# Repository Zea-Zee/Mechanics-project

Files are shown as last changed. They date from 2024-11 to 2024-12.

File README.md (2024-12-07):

# Mechanics project
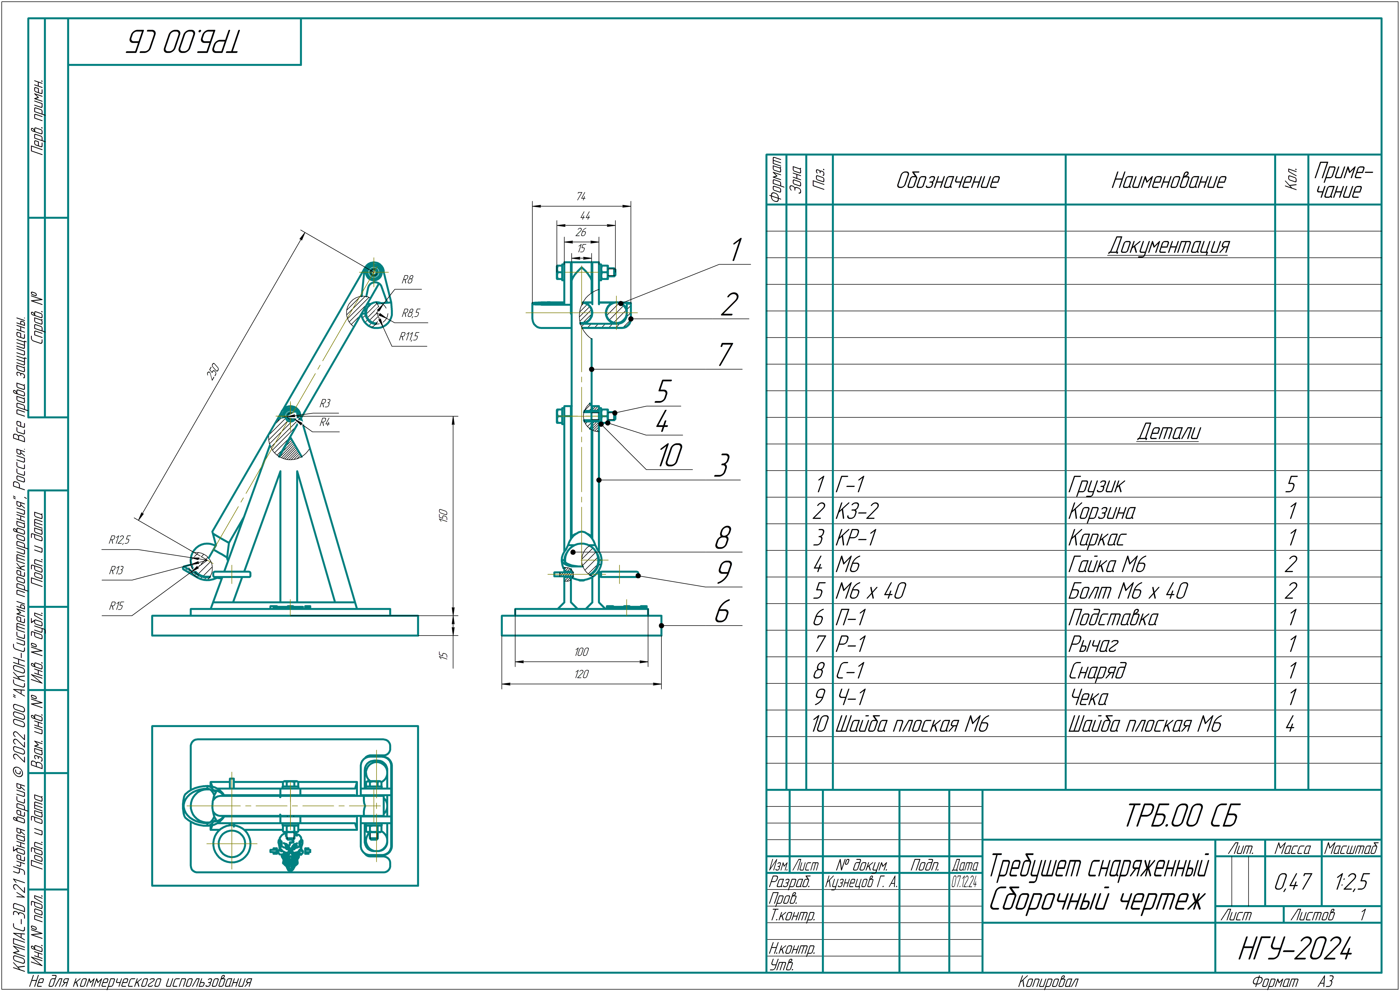
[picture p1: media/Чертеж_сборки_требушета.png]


Дано:

Параметры катапульты:

$$
\alpha_{start}=240^{\circ}\ (начальный\ угол\ снаряда)\\
\alpha_{release}=30^{\circ}\ (угол\ вылета\ снаряда)\\
h_{frame}=0.15м\ (высота\ оси\ вращения\ рычага)\\
l_{arm}=0.25м\ (длина\ всего\ рычага)\\
k_{arm}=0.5\ (соотношение\ плеч\ рычага)\\
m_{arm}=0.018кг\ (масса\ всего\ плеча)
$$

Параметры запуска:

$$
m_{missile}=0.016кг\ (масса\ снаряда)\\
d=0.5м\ (расстояние\ которое\ снаряд\ должен\ пролететь\ от\ станины)\\
R_{missile}=0.008м\ (радиус\ снаряда)
$$

Введем некоторые переменные: (лучше не читать)

$$
\beta_{start\_missile}=\alpha_{start}+90^\circ=240^\circ\ (Угол\ рычага\ снаряда \ в \ начальный\ момент)\\
\beta_{release\_missile}=\alpha_{release}+90^\circ=120^\circ\ (Угол\ рычага\ снаряда \ в \ момент\ вылета )\\
\beta_{start\_weight}=\alpha_{start}+270^\circ=60^\circ\ (Угол\ рычага\ противовеса\ в \ начальный\ момент)\\
\beta_{release\_weight}=\alpha_{release}+270^\circ=300^\circ\ (Угол\ рычага\ противовеса\ в \ момент\ вылета)\\

l_{missile\_arm}=l_{missile}*(1-k_{arm})=0.125м\ (длина\ плеча\ снаряда)\\
l_{weight\_arm}=l_{missile}*k_{arm}=0.125м\ (длина\ плеча\ противовеса)\\
$$

Теперь рассчитаем положения снаряда и противовеса: (лучше не читать)

$$
x_{start\_missile}=\cos(\beta_{start\_missile})*l_{missile\_arm\_length}\\
y_{start\_missile}=\sin(\beta_{start\_missile})*l_{missile\_arm\_length}+h_{frame}\\

x_{start\_weight}=\cos(\beta_{start\_weight})*l_{_weight\_arm\_length}\\
y_{start\_weight}=\sin(\beta_{start\_weight})*l_{_weight\_arm\_length}+h_{frame}\\

x_{release\_missile}=\cos(\beta_{release\_missile})*l_{missile\_arm\_length}\\
y_{release\_missile}=\sin(\beta_{release\_missile})*l_{missile\_arm\_length}+h_{frame}\\

x_{release\_weight}=\cos(\beta_{release\_weight})*l_{_weight\_arm\_length}\\
y_{release\_weight}=\sin(\beta_{release\_weight})*l_{_weight\_arm\_length}+h_{frame}
$$

Рассчитаем начальную скорость v0 под углом вылета:

$$
x=x_{start\_missile}+v_0\cos(\alpha_{release})t\\

y=y_{start\_missile}+v_0\sin(\alpha_{release})t-\frac{gt^2}{2}\\
\\

Выразим\ t\ через\ x\\
t=\frac{x-x_{start\_missile}}{v_0\cos(\alpha_{release})}\\

Подставим\ в\ y\\
y=y_{start\_missile}+v_0\sin(\alpha_{release})(\frac{x-x_{start\_missile}}{v_0\cos(\alpha_{release})})-\frac{g(\frac{x-x_{start\_missile}}{v_0\cos(\alpha_{release})})^2}{2}\\

Упростим\\
y=y_{start\_missile}+(x-x_{start\_missile})\tan(\alpha_{release})-\frac{g(x-x_{start\_missile})^2}{2v_0\cos(\alpha_{release})}\\
\\

Выразим\ v_0\\
v_0=\frac{g(x-x_{start\_missile})^2}{2\cos^2(\alpha_{release})[(x-x_{start\_missile})\tan(\alpha_{release})-(y-y_{start\_missile})]}\\

Посчитаем\ v_0\\
v_0=\frac{9.81м/с^2 * (0.5м-(-0.0625м))^2}{2*0.75*[(0.5м-(-0.0625м))*0,578-(0м-0.258м)]}=1.90м/с
$$

Теперь выведем время полета, и закон движения:

$$
v_x=v_0\cos(\alpha_{release})=1.64м/с\ (скорость\ снаряда\ по\ x)\\
v_y=v_0\sin(\alpha_{release})=0.95м/с\ (скорость\ снаряда\ по\ y)\\

t_{path1}=\frac{v_y}{g}=0.0967с\ (время\ полета\ до\ наивысшей\ точки)\\
y_{max}=y_{release\_missile}+v_yt_{path1}-\frac{gt_{path1}^2}{2}=0.304м\ (наивысшая \ точка\ полета)\\
Из\ закона\ движения\ y\ выразим\ \\
t_{path2}=\frac{\sqrt{2y_{max}}}{g}=0.249с\\
t_{tot}=t_{path1}+t_{path2}=0.3456с
$$

Missile start point: (-0.06250000000000006; 0.041746824526945184)
Weight start point: (0.06250000000000006; 0.2582531754730548)
Missile release point: (-0.06249999999999997; 0.2582531754730548)
Weight release point: (0.06249999999999997; 0.041746824526945156)
239.99999999999997 119.99999999999999
0.21650635094610965
Launching missile with angle: 30.00 degrees and v0: 1.88 m/s
Weight mass: 0.03438221420742506
Vx: 1.6312813025047181, Vy: 0.9418206991251022
first_path_time 0.09603898366160742
max_y 0.3034789268407745
second_path_time 0.24878198568090912
total_time 0.34482096934251655
Flight time: 0.34482096934251655 s, x_move: 0.5624999999999999 m, y_move: -0.25825317547305493 m
Landed in: (0.4999999999999999; -1.1102230246251565e-16)

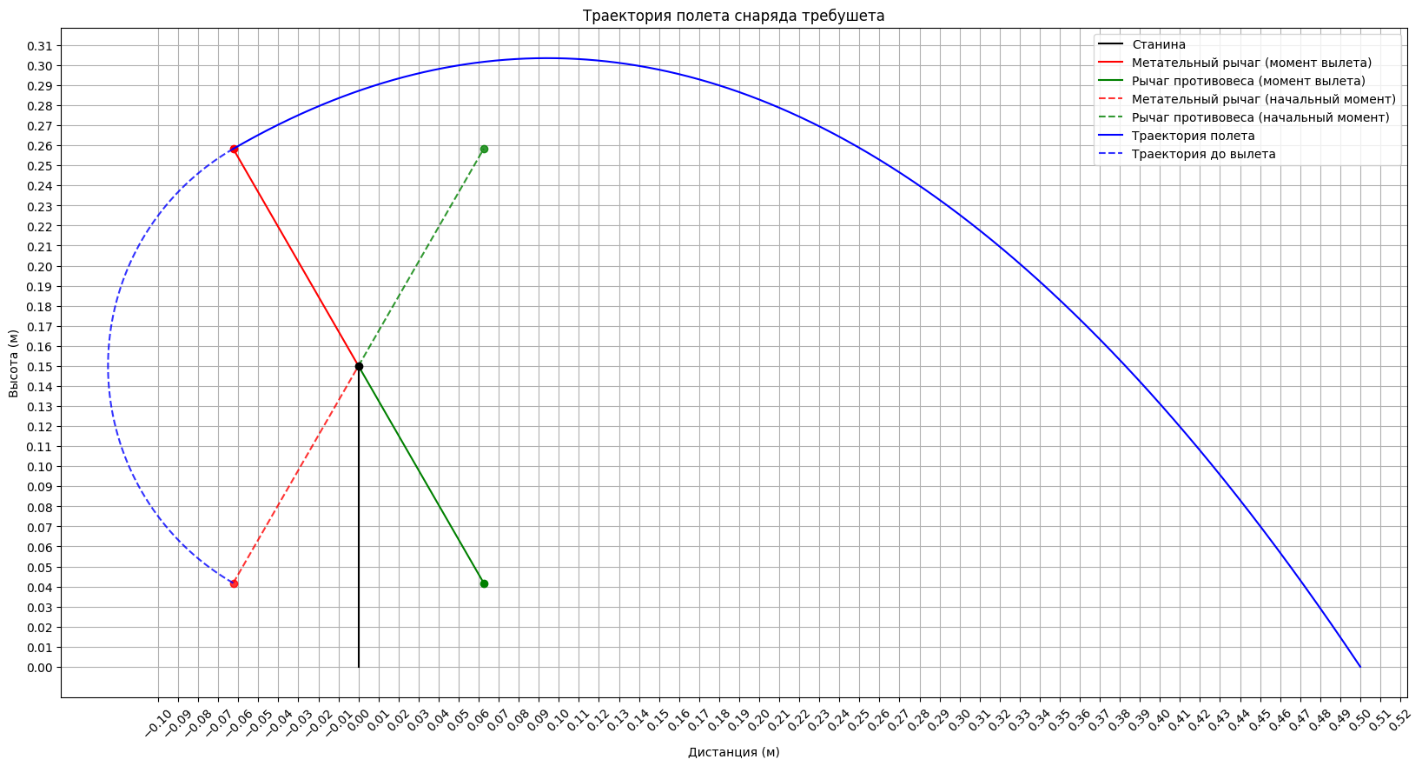
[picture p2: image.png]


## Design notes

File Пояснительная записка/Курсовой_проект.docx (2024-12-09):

МИНИСТЕРСТВО НАУКИ И ВЫСШЕГО ОБРАЗОВАНИЯ
РОССИЙСКОЙ ФЕДЕРАЦИИ

НОВОСИБИРСКИЙ ГОСУДАРСТВЕННЫЙ УНИВЕРСИТЕТ

Курсовая проект по дисциплине:

«МЕХАНИКА»

Проектирование механической модели требушета

Факультет: Институт Интеллектуальной Робототехники

Группа: 22932

Студенты: | Оценка
Кадиленко Иван
Кузнецов Глеб

Преподаватель: Сахнов А.Ю.

НОВОСИБИРСК

2024

1. Задание на курсовую работу.

1. Метание деформируемого снаряда любой выбранной массы и формы на расстояние от 30 см до 60 см и отклонением от центральной оси не более 30°.

2. Нахождение модели во взведённом состоянии без приложения посторонних сил (без помощи человека).

3. Механический спуск.

4. Целостность и устойчивость конструкции в течение 3-х попыток метания.

2. Эскиз модели.

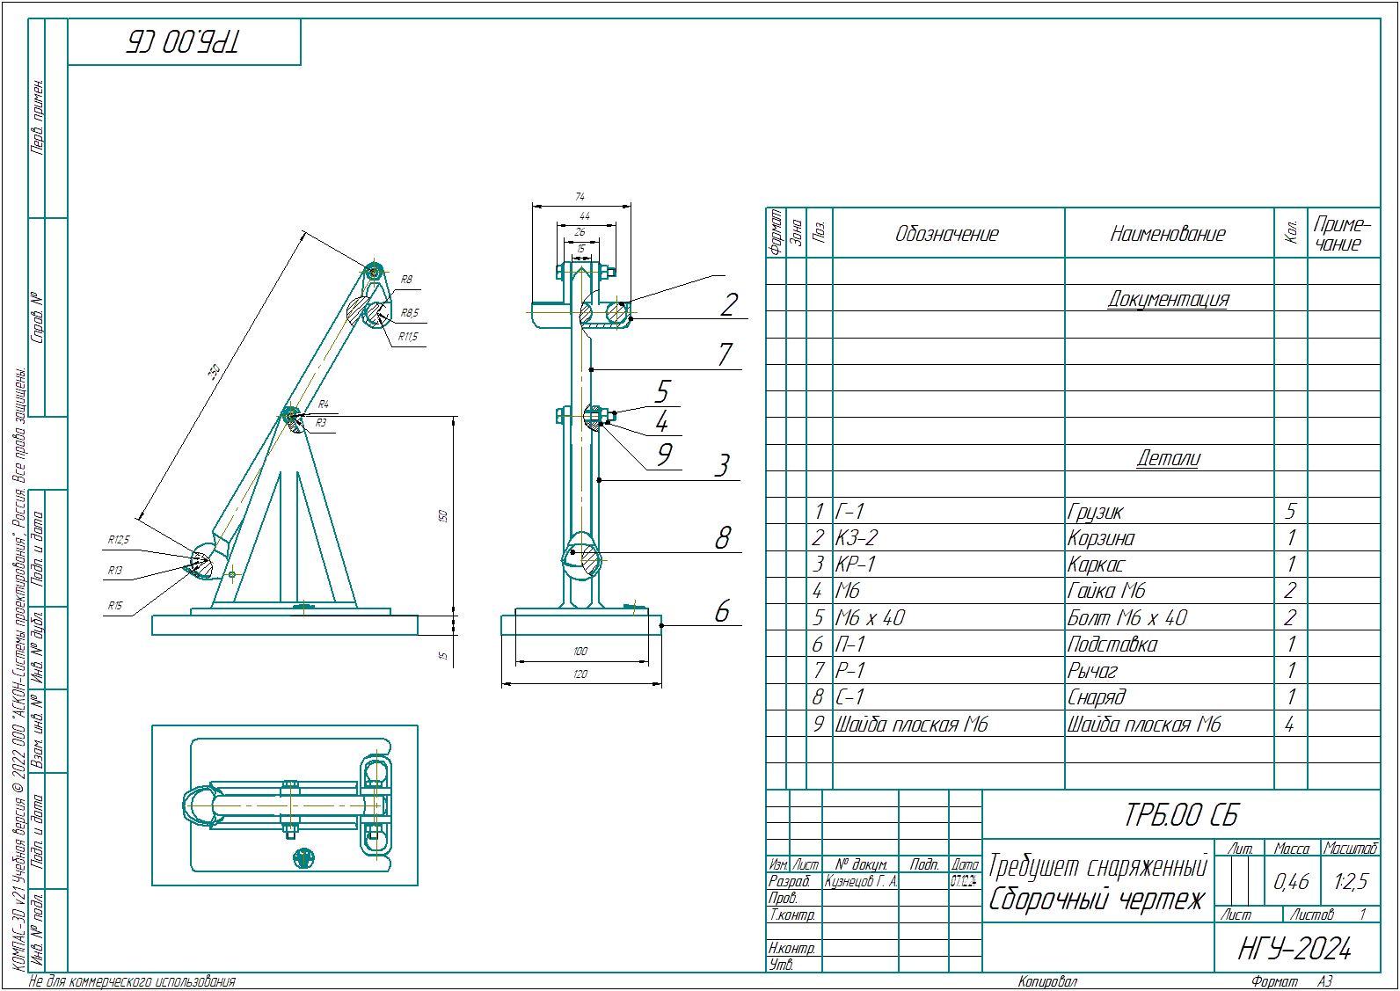
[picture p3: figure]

Рисунок 1. Чертёж модели. Размеры в мм

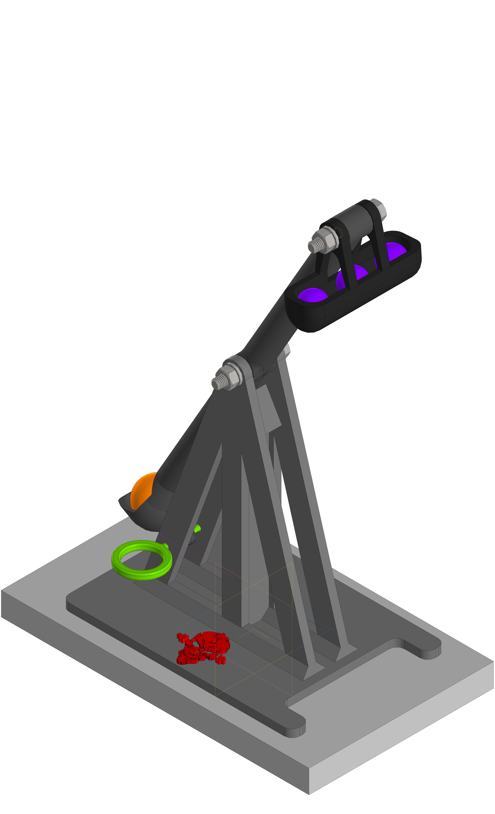
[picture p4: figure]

Рисунок 2. Модель требушета в изометрии.

3. Динамический анализ механической модели (Расчёт разгона снаряда)

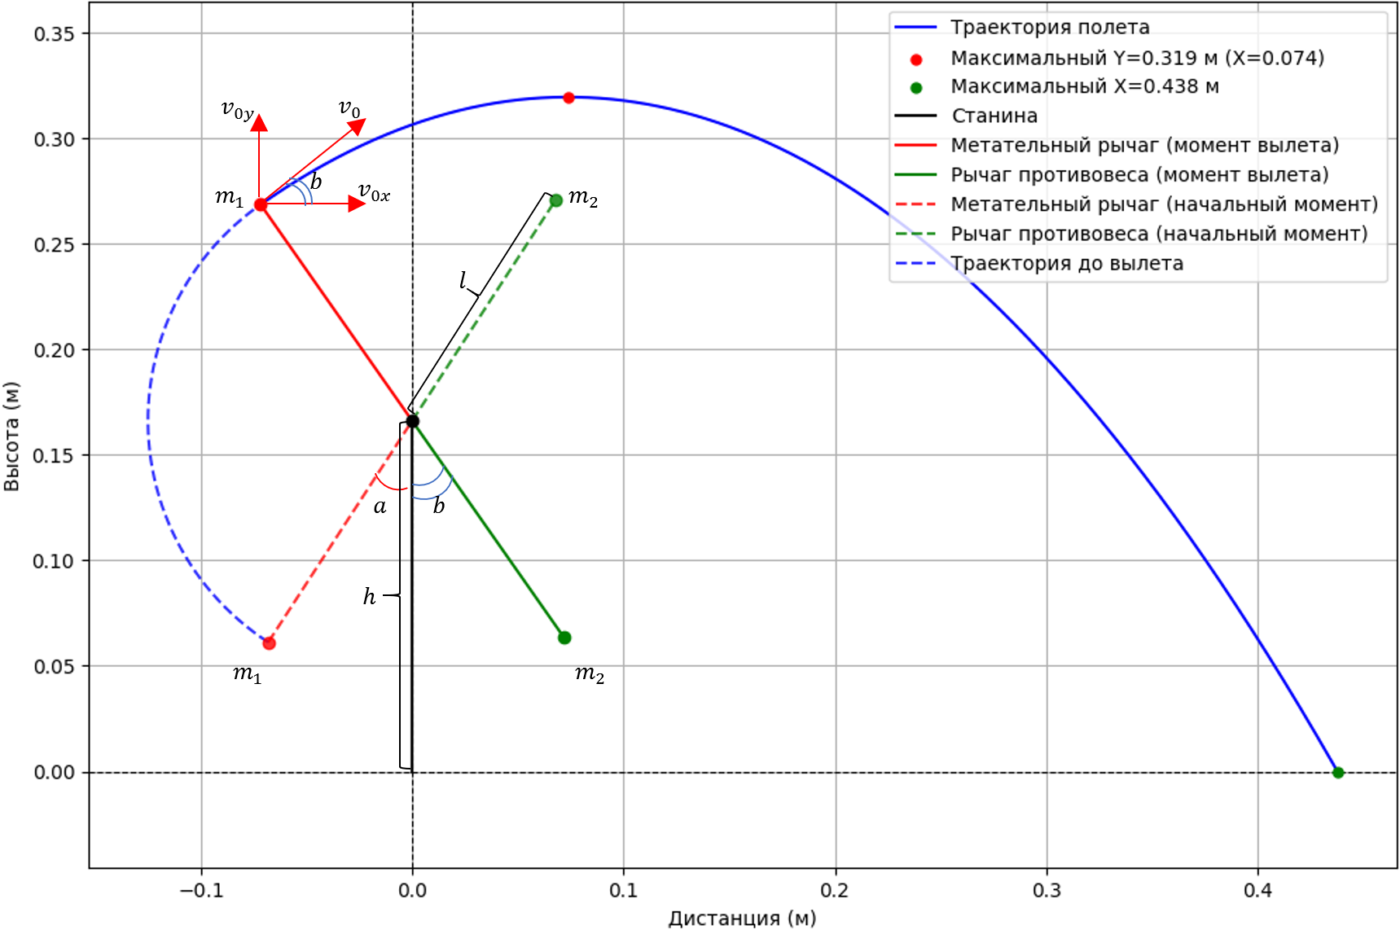
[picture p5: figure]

Рисунок 3. Схема работы требушета с параметрами.

Введём переменные, которые потребуются для расчётов, в скобках указаны значения нашего требушета:

m_1 – Масса снаряда (0.0111 кг)

m_2 – Масса противовеса (0.0765 кг)

m_r – Масса рычага (0.019 кг)

l – Расстояние от конца рычага до оси вращения (0.125 м)

g – Ускорение свободного падения (9.81 м/c^2 )

a – Стартовый угол (33°)

b – Угол вылета (35°)

b' - Угол вылета, измеренный в ту же сторону что и стартовый угол (145°)

Для нахождения скорости вылета снаряда, запишем уравнение баланса энергий для начального момента и момента вылета

E_(Im_2)^п =E_(IIm_1)^п +E_(IIm_1)^к +E_(IIm_2)^к

h^(') =l*(cos(a)+cos(b)) – Разница высоты между начальным моментом и моментом вылета

E_(Im_2)^п =m_2 *g*h' - Потенциальная энергия снаряда в начальный момент

E_(IIm_1)^п =m_1 *g*h' - Потенциальная энергия снаряда в момент вылета

E_(IIm_1)^к =(m_1 *v^2)/2 – Кинетическая энергия снаряда в момент вылета

E_(IIm_2)^к =(m_2 *v^2)/2 – Кинетическая энергия противовеса в момент вылета. Учитываем мы её т.к. в момент вылета противовес бьётся об ограничитель. Согласно теореме Карно, эта энергия равна кинетической энергии противовеса в момент удара об ограничитель.

Получаем следующее выражение

m_2 *g*h^(') =m_1 *g*h^(') +(m_1 *v^2)/2+(m_2 *v^2)/2

Выразим скорость

v^2 =(2*g*l*h^(') *(m_2 -m_1 ))/(m_2 +m_1)

Подставим h' и получим итоговое уравнение скорости вылета снаряда

v_0 =√((2*g*l*(cos(a)+cos⁡(b))*(m_2 -m_1 ))/(m_2 +m_1))

Подставим наши значения и получим скорость вылета снаряда

v_0 =1.742 м/c

4. Кинематический анализ механической модели (Расчёт траектории полёта снаряда)

Введём переменные, которые потребуются для расчётов, в скобках указаны значения нашего требушета:

v_0 - Скорость снаряда в момент вылета (1.742 м/с)

h - Высота оси вращения (0.15 м)

shift – Смещение от точки пуска по оси Х до оси вращения (0.07 м)

Рассчитаем высоту запуска

h_l =h+l*cos⁡(b)

Рассчитаем время полета снаряда до момента пересечения высоты запуска по оси Y

v_y → -v_y

t_1 =(v_y -(-v_y ))/g=(2v_y)/g=2v_y *(sin(b))/g

Найдём оставшееся время полёта снаряда

h_l =v_y *t+(gt^2)/2

gt^2 +2v*sin(b)-2h_l =0

D=(2*v*sin(b))^2 +8*g*h_l

t_2 =(-2*v*sin(b)+√D)/(2g)

Общее время полёта

t=t_1 +t_2

По X нет ускорения, составим уравнение

x=v_0 *cos(b)*t-shift

Уравнение по Y

y=v_0 *sin(b)*t-1/2*gt^2 +h_l

Подставим скорость вылета снаряда и получим дальность

x=0.438 м

5. Обоснование устойчивости механической модели (Определение центра тяжести)

Проведём теоретический расчёт центра масс требушета. Учитывая симметрию требушета относительно вертикальной плоскости, достаточной найти координаты центра тяжести в проекции на данную плоскость. Формула для нахождения центра масс в общем виде для k элементов:

X=(∑_(i=1)^k X_i *m_i)/(∑_(i=1)^k m_i)

Подставим наши значения (второе слагаем умножено на 3, т.к. мы используем 3 противовеса)

X=(0.168*0.01+0.168*(0.0168*3)+0.104*0.019+0.041*0.0111+0.102*0.066+0.104*0.2755)/(0.01+(0.0168*3)+0.019+0.0111+0.066+0.2755)

Y=(0.253*0.01+0.242*(0.0168*3)+0.165*0.019+0.057*0.0111+0.07*0.066+0.0075*0.2755)/(0.01+(0.0168*3)+0.019+0.0111+0.066+0.2755)

Вычислим значения центра масс

X≈0.111 м

Y≈0.06 м

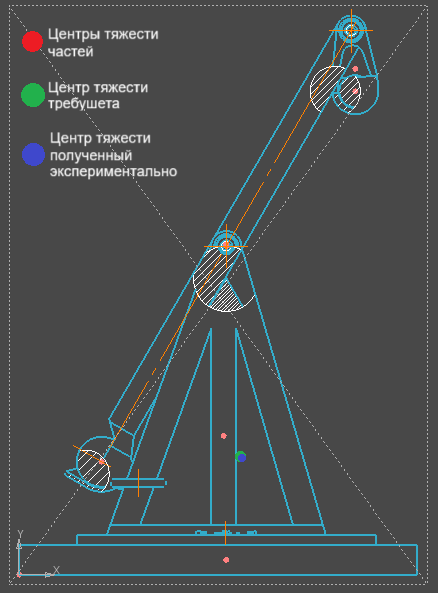
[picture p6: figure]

Рисунок 4. Теоретически рассчитанный центр масс требушета

Рассчитаем центр масс экспериментально методом подвешивания.

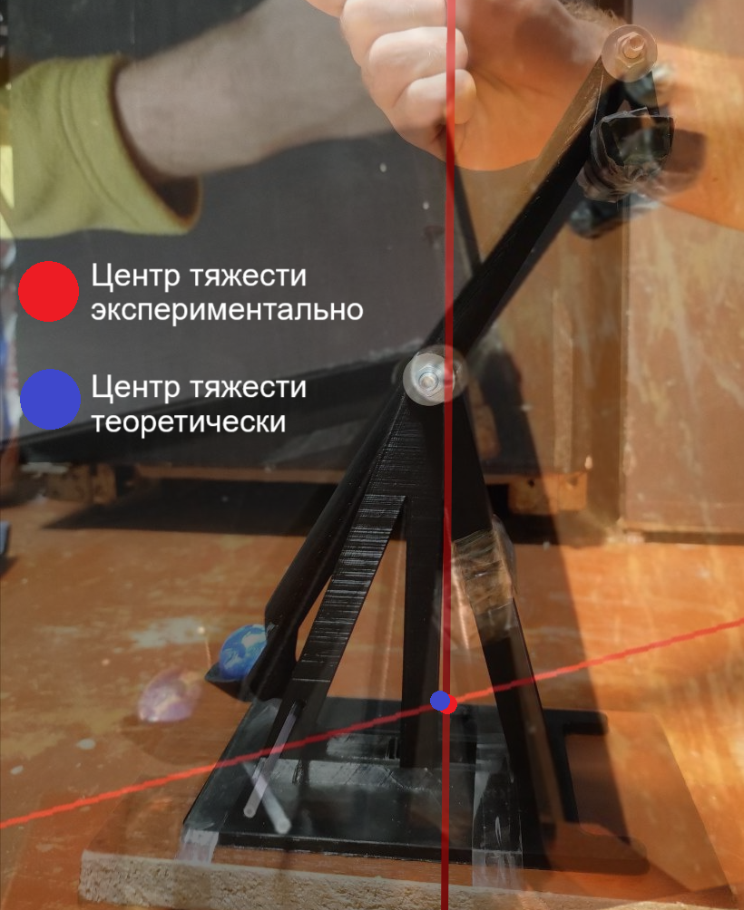
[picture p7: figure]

Рисунок 5. Экспериментально рассчитанный центр тяжести требушета.

Как можно увидеть мы получили достаточно точное совпадение центров тяжести.

6. Сравнение фактических параметров механической модели с расчётными параметрами.

Проведя 3 пуска, были получены следующие результаты: 0.475 м, 0.45 м, 0.48 м.

X_(факт) =(0.475+0.45+0.48)/3=0.468 м

Рассчитаем абсолютную и относительную погрешности

ΔX_(абс) =0.468-0.438=0.03 м

δ=(0.468-0.438)/0.468*100%=6.48%

Такая разница в фактические и расчётные значения может быть вызвана тем, что мы учитываем удар плеча об ограничитель как абсолютно неупругий удар, что может быть не совсем верно.

7. Описание электронной модели механической системы

Программа запускается при помощи python, на вход её подаются все значения, нужные для расчёта. Если никакие значения не будут переданы, будут взяты значения нашего требушета.

Запуск: py calculation.py

Передаваемые параметры:

--m1 - Масса снаряда.

--m2 – Масса противовеса

--h – Высота оси вращения

--l – Длина плеча (от оси до края рычага).

--alpha – Начальный угол

--beta – Угол вылета

--is_shift - Учитывать ли смещение точки вылета по X относительно оси вращения.

--visualize - Выводить ли визуализацию.

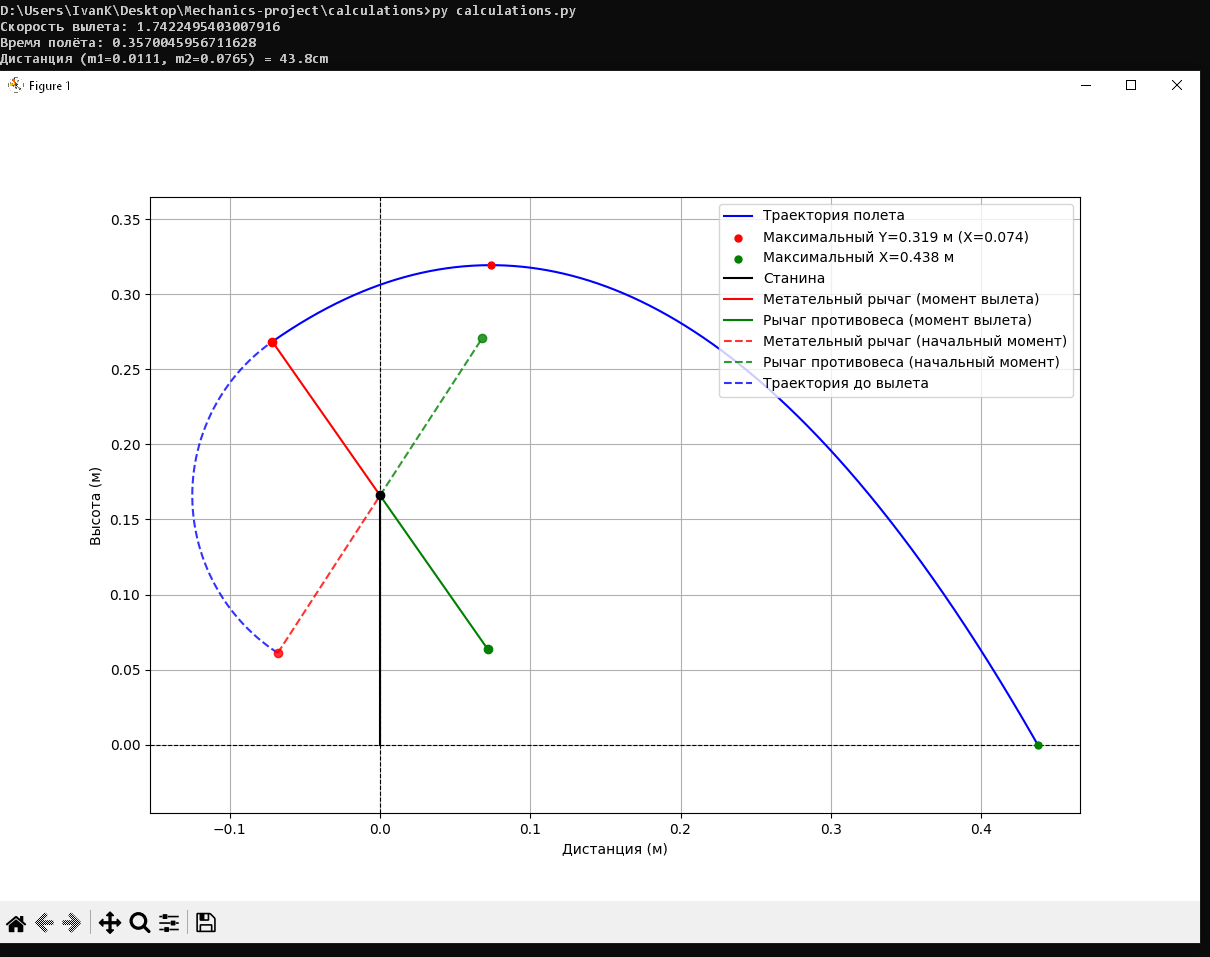
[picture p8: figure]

Рисунок 6. Пример работы программы.

Листинг кода:

import math

import numpy as np

import matplotlib.pyplot as plt

import argparse

G = 9.81

def calculate_r(m1, m2, ma, h, l, a1, a2, is_shift=False, visualize=False):

'''

m1 - mass of projectile \n

m2 - mass of counterweight \n

ma - mass of lever \n

h - height of mount \n

l - length of lever \n

a1 - start angle \n

a2 - finish angle (Measured in the opposite direction from the starting point) \n

shift - difference between middle of trebushet and position of throw \n

visualise - visualise trajectory \n

'''

a1r = np.radians(a1)

a2r = np.radians(a2)

speed = np.sqrt((2*G*l*(np.cos(a1r) + np.cos(a2r))*(m2-m1))/(m1+m2))

print('Скорость вылета:', speed)

t1 = (2*speed*np.sin(a2r))/G

x1 = t1*speed*np.cos(a2r)

heigth_of_launch = h + l*np.cos(a2r)

D = (2*speed*np.sin(a2r))**2 + 8*G*(heigth_of_launch)

t2 = (-2*speed*np.sin(a2r) + np.sqrt(D))/(2*G)

x2 = speed*np.cos(a2r)*t2

print('Время полёта:', t1+t2)

length = x1+x2

if is_shift:

shift = l * np.sin(a2r)

length -= shift

else:

shift = 0

print(f'Дистанция (m1={m1}, m2={m2}) = {length*100:.1f}cm')

if visualize:

t1_arr = np.linspace(0, t1+t2, num=10000, endpoint=False)

x1_arr = speed*np.cos(a2r)*t1_arr - shift

y1_arr = speed*np.sin(a2r)*t1_arr - 1/2*G*(t1_arr**2) + heigth_of_launch

plt.figure(figsize=(12,8))

plt.plot(x1_arr, y1_arr, color='blue', label='Траектория полета')

plt.scatter(x1_arr[np.where(y1_arr == np.max(y1_arr))][0], np.max(y1_arr), color='red', s=25, zorder=10, label=f'Максимальный Y={np.max(y1_arr):.3f} м (X={x1_arr[np.where(y1_arr == np.max(y1_arr))][0]:.3f})')

plt.scatter(x1_arr[-1], 0, color='green', s=25, zorder=10, label=f'Максимальный X={x1_arr[-1]:.3f} м')

plt.plot([0, 0], [0, h], label='Станина', color="black")

plt.plot([-l*np.sin(a2r), 0], [h+l*np.cos(a2r), h], label='Метательный рычаг (момент вылета)', color='red')

plt.plot([0, l*np.sin(a2r)], [h, h-l*np.cos(a2r)], label='Рычаг противовеса (момент вылета)', color='green')

plt.plot([-l*np.sin(a1r), 0], [h-l*np.cos(a1r), h], label='Метательный рычаг (начальный момент)', color='red', linestyle='--', alpha=0.8)

plt.plot([0, l*np.sin(a1r)], [h, h+l*np.cos(a1r)], label='Рычаг противовеса (начальный момент)', color='green', linestyle='--', alpha=0.8)

plt.plot(0, h, marker='o', color='black')

plt.plot(-l*np.sin(a2r), h+l*np.cos(a2r), marker='o', zorder=10, color='red')

plt.plot(l*np.sin(a2r), h-l*np.cos(a2r), marker='o', zorder=10, color='green')

plt.plot(-l*np.sin(a1r), h-l*np.cos(a1r), marker='o', zorder=10, color='red', alpha=0.8)

plt.plot(l*np.sin(a1r), h+l*np.cos(a1r), marker='o', zorder=10, color='green', alpha=0.8)

pre_release_t = np.linspace(np.radians(270-a1), np.radians(90+a2), num=1000)

pre_release_x = np.cos(pre_release_t) * l

pre_release_y = h + np.sin(pre_release_t) * l

plt.plot(pre_release_x, pre_release_y, label='Траектория до вылета', color='blue', linestyle='--', alpha=0.8)

plt.axhline(0, color='black', linestyle='--', linewidth=0.8)

plt.axvline(0, color='black', linestyle='--', linewidth=0.8)

plt.xlabel('Дистанция (м)')

plt.ylabel('Высота (м)')

plt.legend(loc='upper right')

plt.grid()

plt.axis('equal')

plt.show()

return length

def main():

ball = 0.0168

jump_ball = 0.0111

fixing = 0.009 + 0.0025 + 0.0025 * 2 #= 0.0165

backet = [0.010, 0.027, 0.043, 0.060, 0.077]

lever_mass = 0.019

frame_mass = 0.066

# Длины в метрах

lever_length = 0.125

frame_heigth = 0.151

bruss_heigth = 0.015

# Углы в градусах

alpha = 33

beta = 35

parser = argparse.ArgumentParser()

parser.add_argument("--m1", default=jump_ball,

help="Масса снаряда.", type=float)

parser.add_argument("--m2", default=backet[3]+fixing,

help="Масса противовеса.", type=float)

parser.add_argument("--ma", default=lever_mass,

help="Масса рычага.", type=float)

parser.add_argument("--h", default=frame_heigth + bruss_heigth,

help="Высота оси вращения.", type=float)

parser.add_argument("--l", default=lever_length,

help="Длина плеча (от оси до края рычага).", type=float)

parser.add_argument("--alpha", default=alpha,

help="Начальный угол.", type=float)

parser.add_argument("--beta", default=beta,

help="Угол вылета.", type=float)

parser.add_argument("--is_shift", default=True,

help="Учитывать ли смещение точки вылета по X относительно оси вращения.", type=bool)

parser.add_argument("--visualize", default=True,

help="Выводить ли визуализацию.", type=bool)

m1 = parser.parse_args().m1

m2 = parser.parse_args().m2

ma = parser.parse_args().ma

h = parser.parse_args().h

l = parser.parse_args().l

a1 = parser.parse_args().alpha

a2 = parser.parse_args().beta

is_shift = parser.parse_args().is_shift

visualize = parser.parse_args().visualize

calculate_r(m1, m2, ma, h, l, a1, a2, is_shift, visualize)

if __name__ == "__main__":

main()

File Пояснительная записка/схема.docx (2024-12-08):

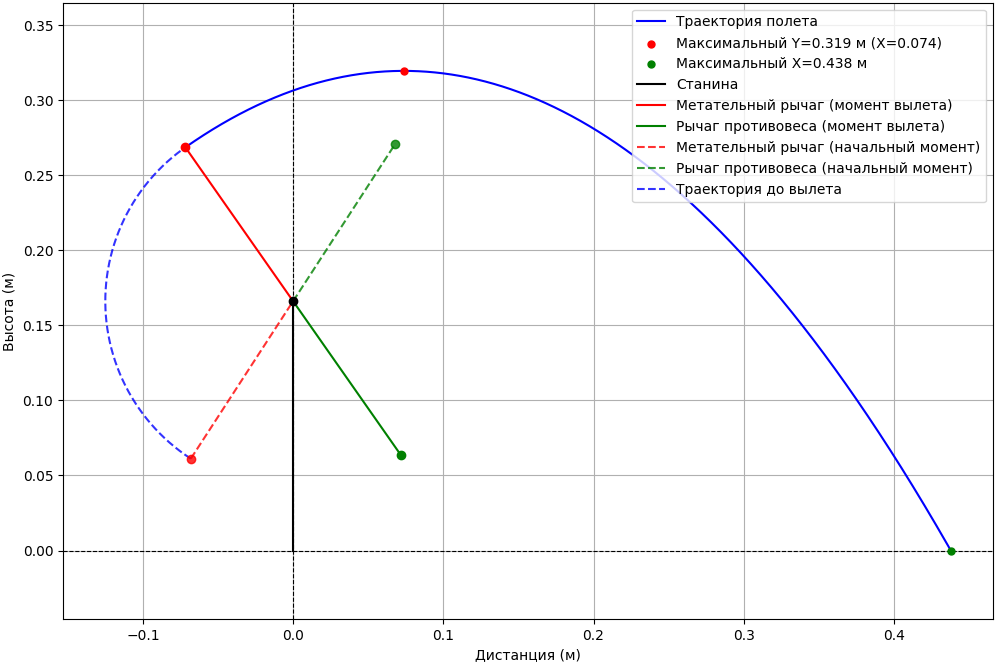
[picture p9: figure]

b

v_(0x)

v_0

v_(0y)

h

l

m_1 m_2

m_1 m_2

a b

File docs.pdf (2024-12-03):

Mechanics project | 1

# Mechanics project

## Дано:

## Параметры катапульты:

## Параметры запуска:

## Введем некоторые переменные: (лучше не читать)

## Теперь рассчитаем положения снаряда и противовеса: (лучше не читать)

## Рассчитаем начальную скорость v0 под углом вылета:

# αstart = 240 (начальный угол снаряда)

∘

# αrelease = 30 (угол вылета снаряда)

∘

# hf rame = 0.15м (высота оси вращения рычага) larm = 0.25м (длина всего рычага) karm = 0.5 (соотношение плеч рычага) marm = 0.018кг (масса всего плеча)

# mmissile = 0.016кг (масса снаряда) d = 0.5м (расстояние которое снаряд должен пролететь от станины) Rmissile = 0.008м (радиус снаряда)

βstart_missile = αstart + 90 =

# ∘ 240 (Угол рычага снаряда в начальный момент)

∘

βrelease_missile = αrelease + 90 =

# ∘ 120 (Угол рычага снаряда в момент вылета)

∘

βstart_weight = αstart + 270 =

# ∘ 60 (Угол рычага противовеса в начальный момент)

∘

βrelease_weight = αrelease + 270 =

# ∘ 300 (Угол рычага противовеса в момент вылета)

∘

lmissile_arm = lmissile ∗ (1 − karm) = 0.125м (длина плеча снаряда)

# lweight_arm = lmissile ∗ karm = 0.125м (длина плеча противовеса)

xstart_missile = cos(βstart_missile ) ∗ lmissile_arm_length

ystart_missile = sin(βstart_missile ) ∗ lmissile_arm_length + hf rame

xstart_weight = cos(βstart_weight) ∗ lweight_arm_length

ystart_weight = sin(βstart_weight) ∗ lweight_arm_length + hf rame

xrelease_missile = cos(βrelease_missile ) ∗ lmissile_arm_length

yrelease_missile = sin(βrelease_missile ) ∗ lmissile_arm_length + hf rame

xrelease_weight = cos(βrelease_weight) ∗ lweight_arm_length

yrelease_weight = sin(βrelease_weight) ∗ lweight_arm_length + hf rame

## Теперь выведем время полета, и закон движения:

## Missile start point: (-0.06250000000000006; 0.041746824526945184) Weight start point: (0.06250000000000006; 0.2582531754730548) Missile release point: (-0.06249999999999997; 0.2582531754730548) Weight release point: (0.06249999999999997; 0.041746824526945156)

239.99999999999997 119.99999999999999
0.21650635094610965

## Launching missile with angle: 30.00 degrees and v0: 1.88 m/s Weight mass: 0.03438221420742506

x = xstart_missile + v0 cos(αrelease )t

y = ystart_missile + v0 sin(αrelease )t −
2

gt

2

# Выразим t через x

t =
v0 cos(αrelease )

x − xstart_missile

# Подставим в y

y = ystart_missile + v0 sin(αrelease )( | ) −
v0 cos(αrelease )

x − xstart_missile
2
g( | )
v0 cos(αrelease )

x−xstart_missile 2

# Упростим

y = ystart_missile + (x − xstart_missile )tan(αrelease ) − 2v0 cos(αrelease )

g(x − xstart_missile )

2

# Выразим v0

v0 =
2 cos (α | )[(x − x | )tan(α | ) − (y − y | )]
2
release | start_missile | release | start_missile
| | g(x − xstart_missile )

2

| | Посчитаем v0
v0 = | =

# 2 ∗ 0.75 ∗ [(0.5м − (−0.0625м)) ∗ 0, 578 − (0м − 0.258м)]

# 9.81м/с ∗ (0.5м − (−0.0625м))

2 2
| | | | 1.90м/с

# vx = v0 cos(αrelease ) = 1.64м/с (скорость снаряда по x) vy = v0 sin(αrelease ) = 0.95м/с (скорость снаряда по y)

tpath1 = =
g
vy | 0.0967с (время полета до наивысшей точки)
ymax = yrelease_missile + vy tpath1 − | =
2

gt
path1

2

# 0.304м (наивысшая точка полета) Из закона движения y выразим

tpath2 = | =
g

# 2ymax 0.249с

ttot = tpath1 + tpath2 = 0.3456с

## Vx: 1.6312813025047181, Vy: 0.9418206991251022 first_path_time 0.09603898366160742 max_y 0.3034789268407745 second_path_time 0.24878198568090912 total_time 0.34482096934251655 Flight time: 0.34482096934251655 s, x_move: 0.5624999999999999 m, y_move:

-0.25825317547305493 m

## Landed in: (0.4999999999999999; -1.1102230246251565e-16)


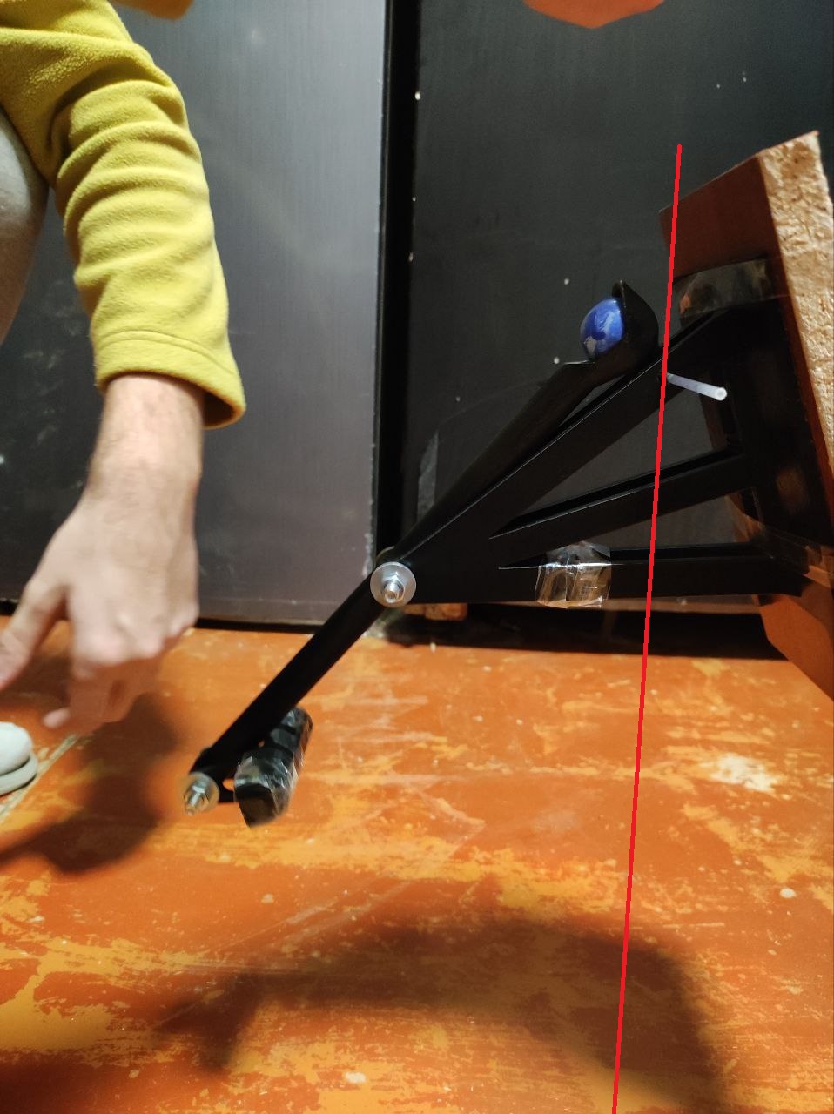
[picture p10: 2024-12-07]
media/Подвес_1.jpg

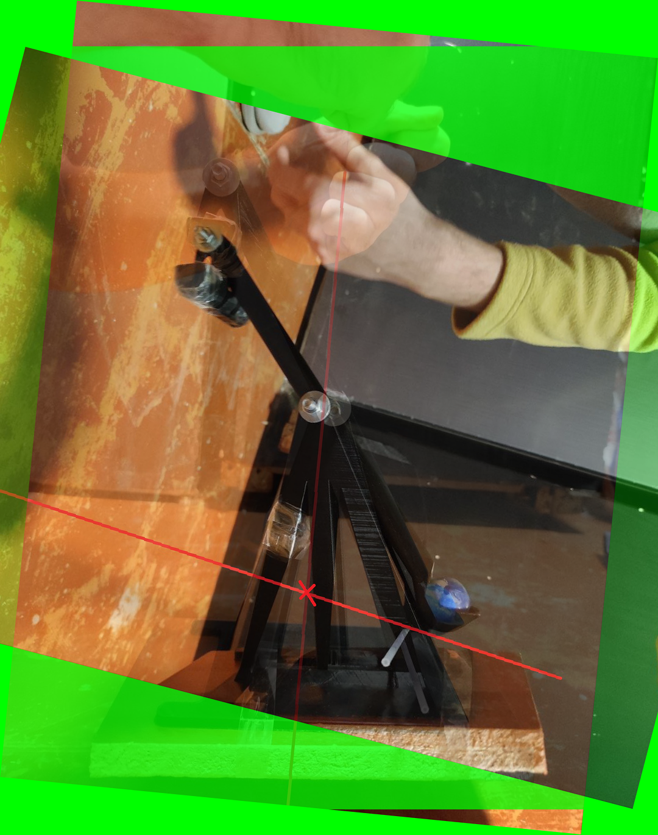
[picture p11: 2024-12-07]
media/Пересечение.png

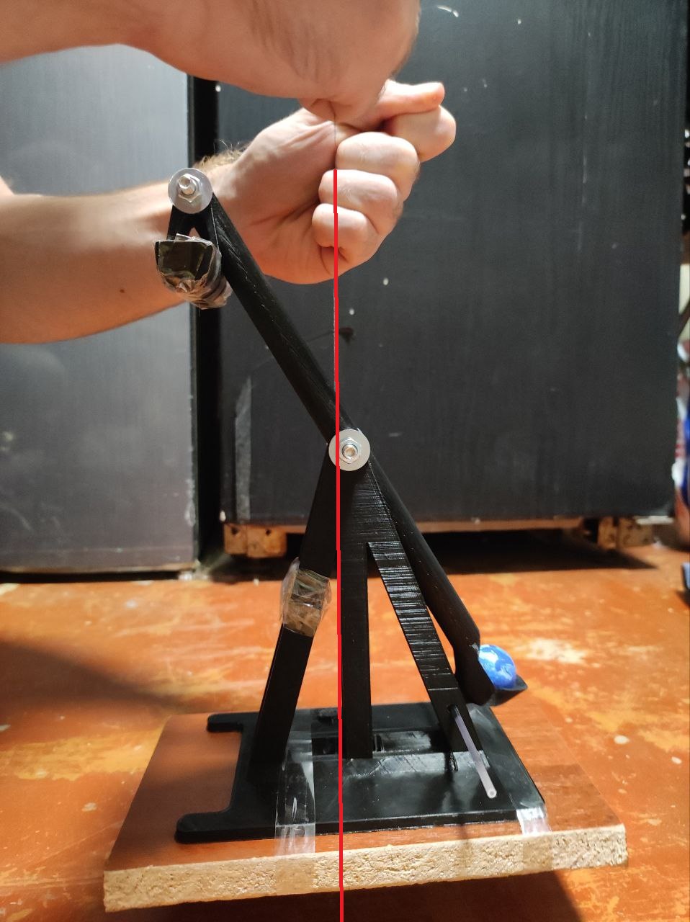
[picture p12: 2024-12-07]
media/Подвес_2.jpg

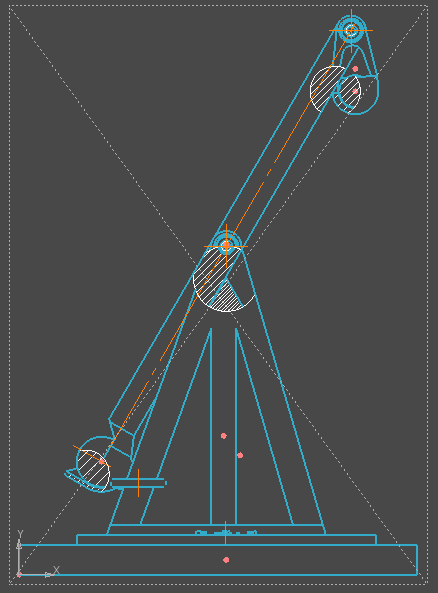
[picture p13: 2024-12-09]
Пояснительная записка/цунтр масс теория + деталей.png

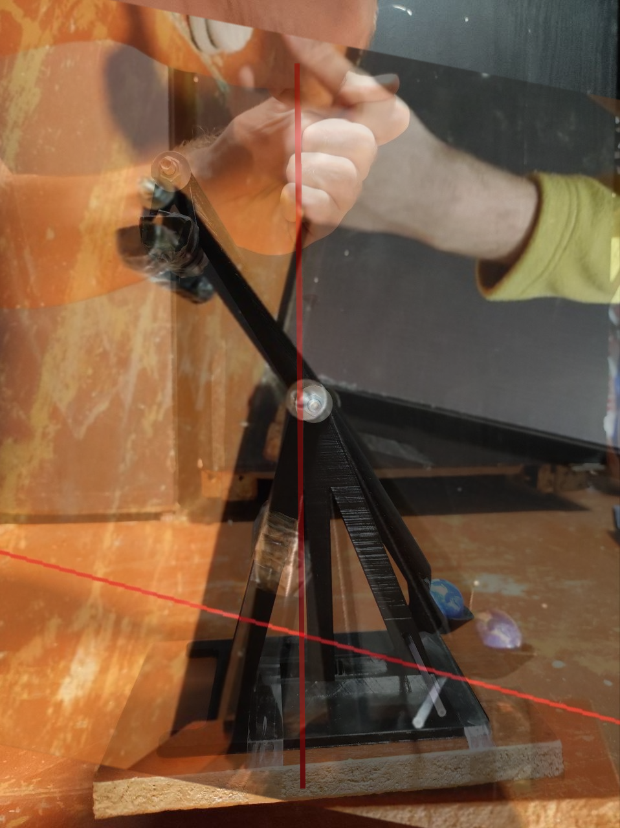
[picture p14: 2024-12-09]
Пояснительная записка/Центр тяжести экспериментально, без точек.png

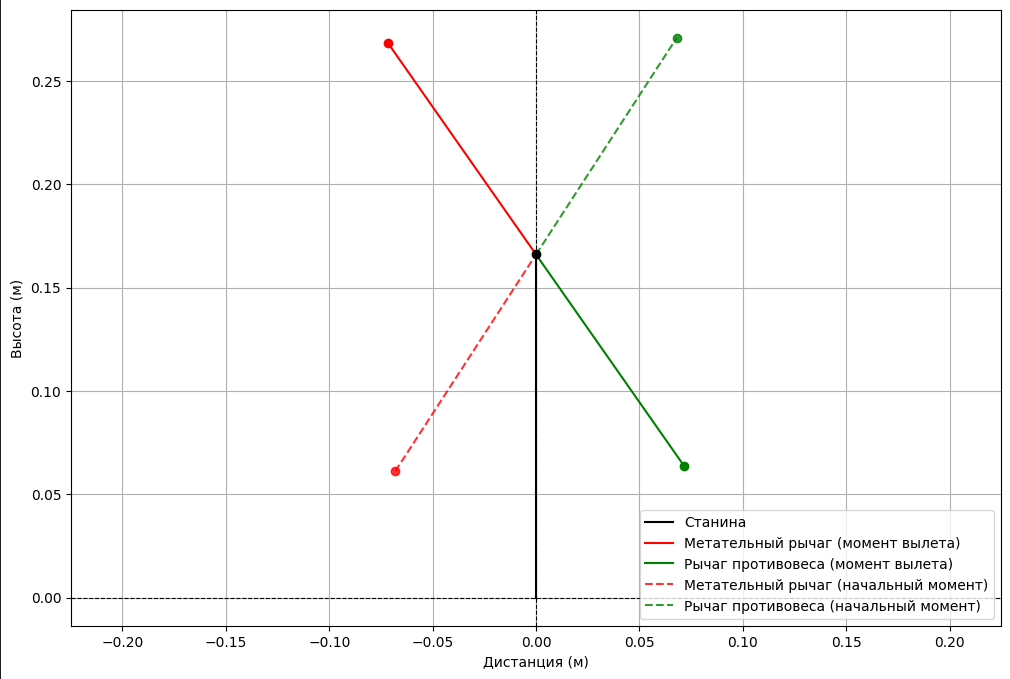
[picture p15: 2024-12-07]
Пояснительная записка/Новый точечный рисунок.bmp

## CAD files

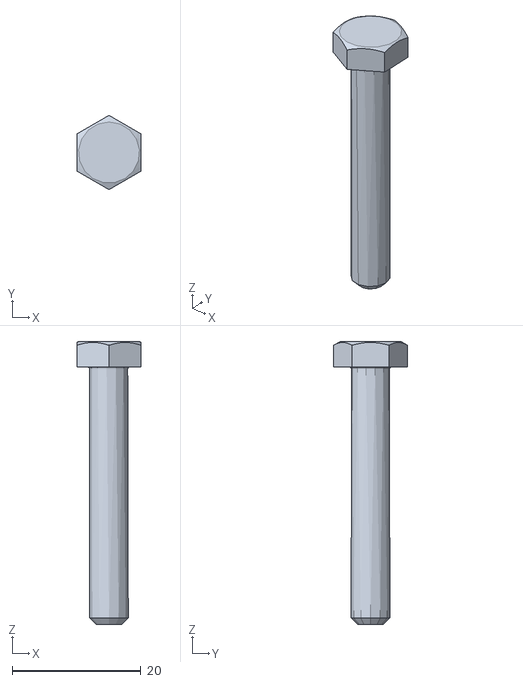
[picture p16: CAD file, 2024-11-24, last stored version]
3d-model/Trebuchet-stl-Kuznetsov/Болт_М6_40_7798-70.stl
10.0 x 11.5 x 44.0

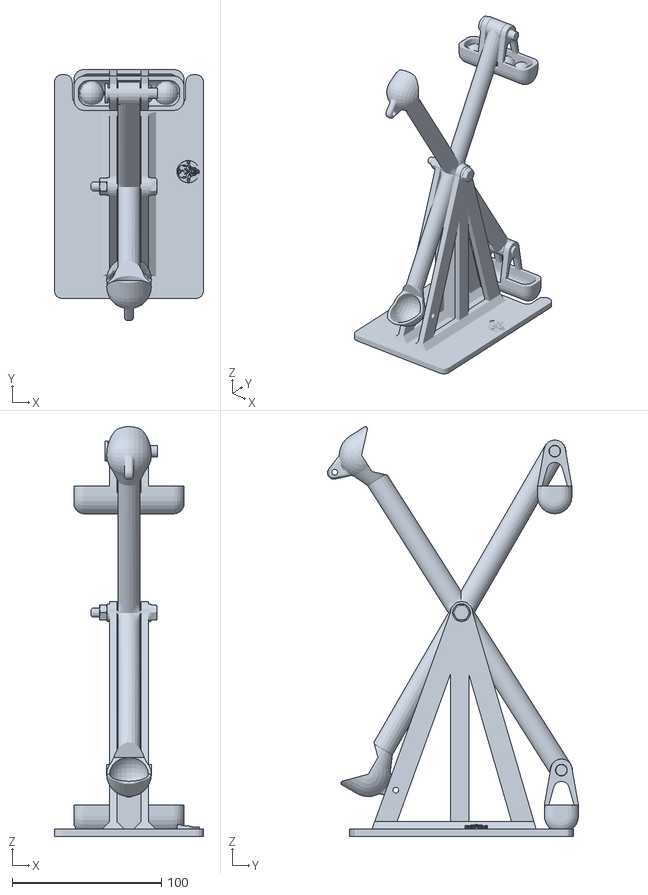
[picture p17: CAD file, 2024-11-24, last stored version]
3d-model/Требушет.stl
100.0 x 168.3 x 274.8

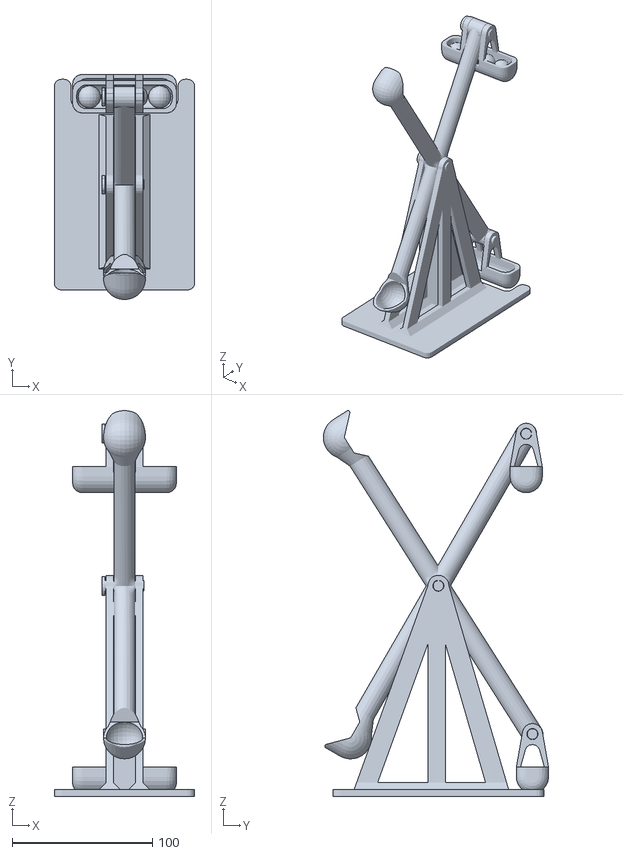
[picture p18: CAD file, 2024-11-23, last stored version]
model.stl
100.0 x 160.3 x 274.8

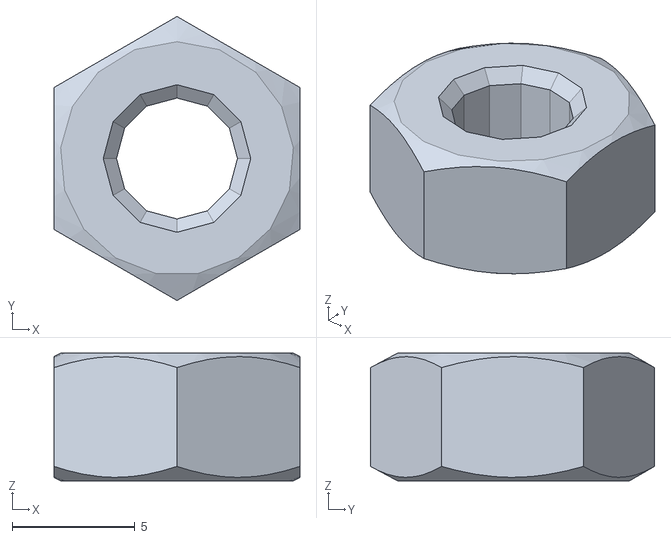
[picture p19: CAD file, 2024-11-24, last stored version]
3d-model/Trebuchet-stl-Kuznetsov/Гайка_М6_5915-70.stl
10.0 x 11.5 x 5.20

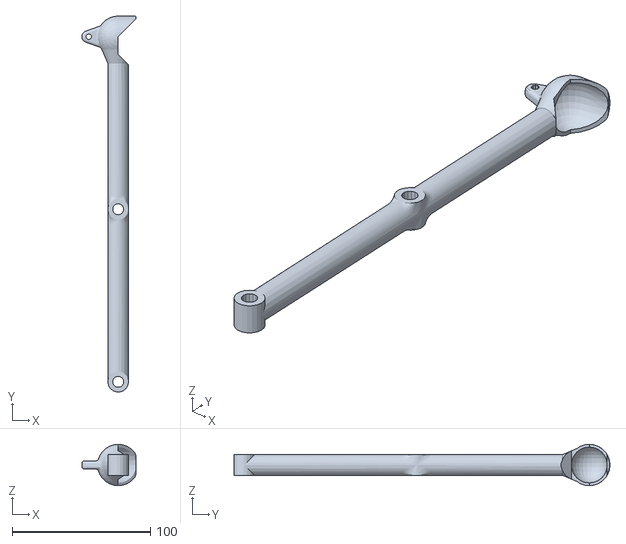
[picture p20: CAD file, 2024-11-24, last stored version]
3d-model/Trebuchet-stl-Kuznetsov/Рычаг.stl
39.3 x 272.4 x 30.0

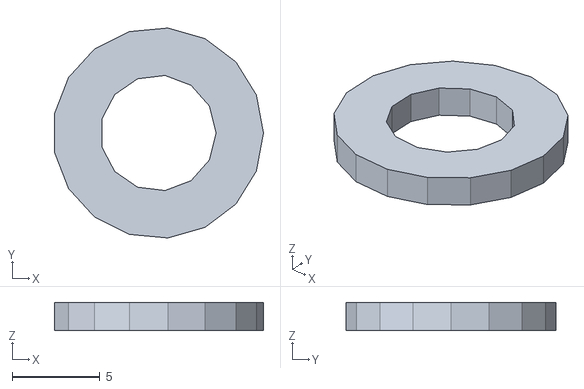
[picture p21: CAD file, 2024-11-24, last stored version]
3d-model/Шайба_6_11371-78.stl
11.9 x 11.9 x 1.60

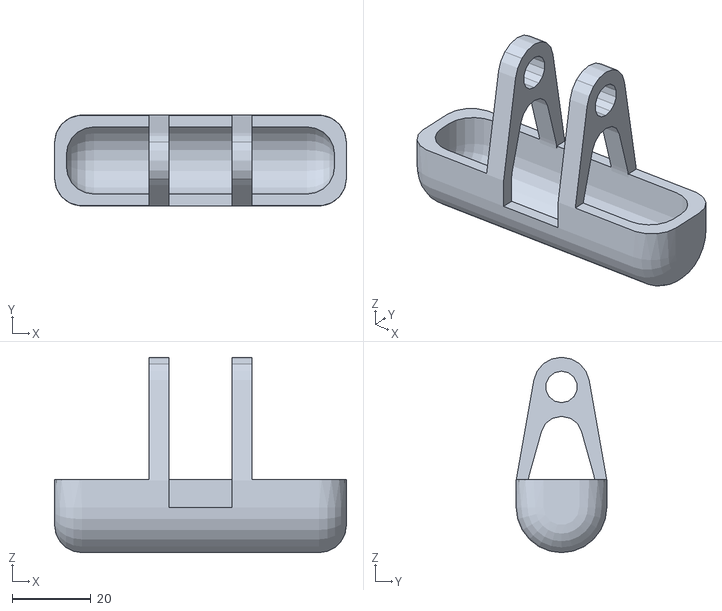
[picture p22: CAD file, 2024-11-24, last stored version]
3d-model/Trebuchet-stl-Kuznetsov/Корзина2.stl
74.0 x 23.0 x 49.5

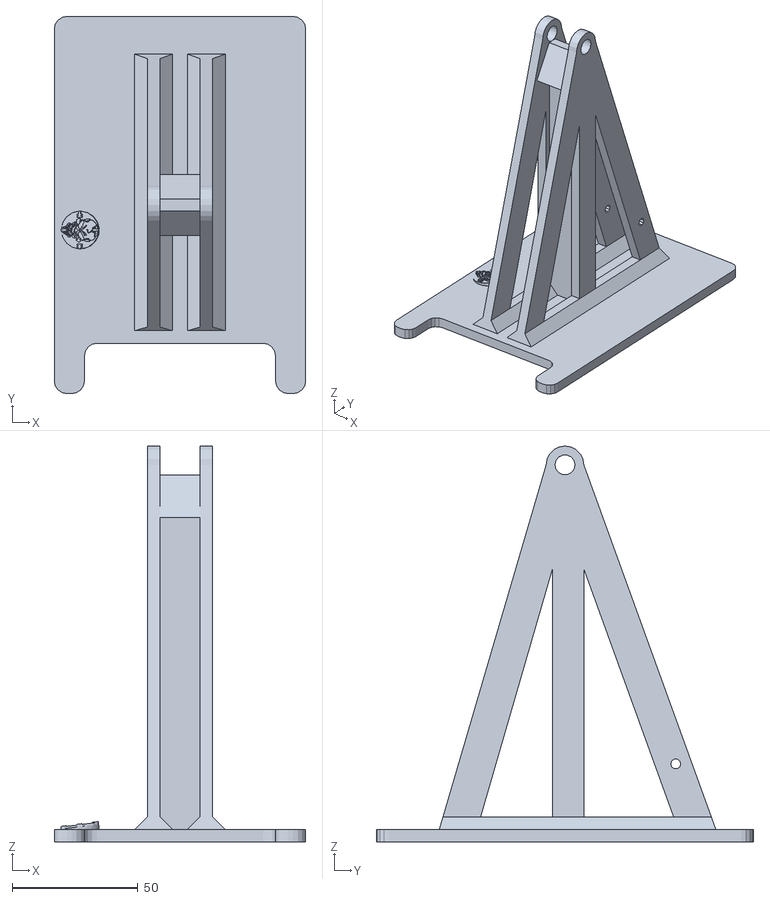
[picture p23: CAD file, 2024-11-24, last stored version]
3d-model/Trebuchet-stl-Kuznetsov/Каркас.stl
100.0 x 150.0 x 157.5

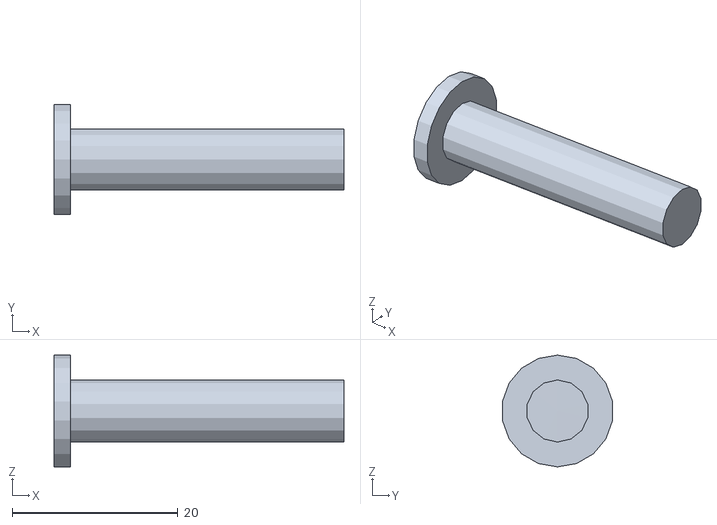
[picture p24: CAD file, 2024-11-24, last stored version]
3d-model/Винт рычага.stl
35.0 x 13.3 x 13.5

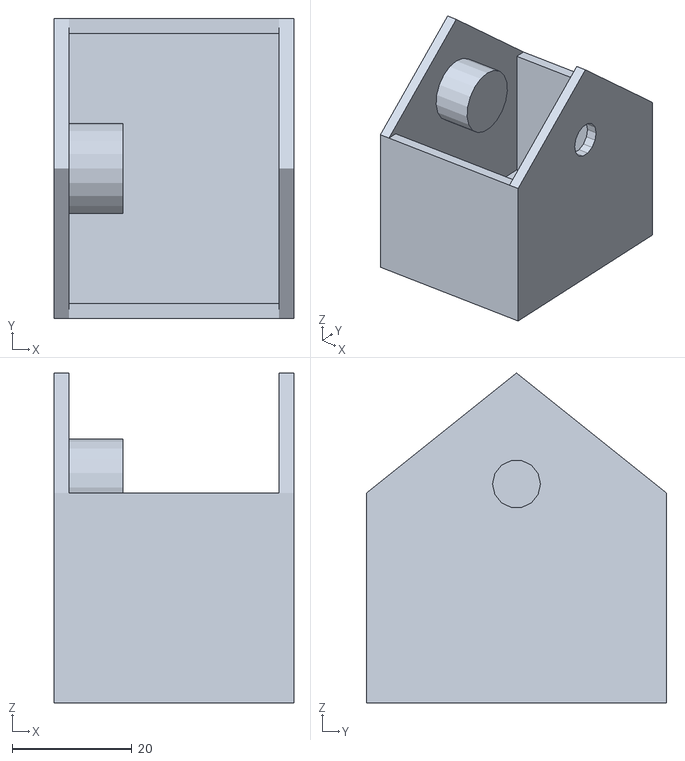
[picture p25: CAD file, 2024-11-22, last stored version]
3d-model/Корзина.stl
40.0 x 50.0 x 55.0

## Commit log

2024-11-21 fully made kinematic
2024-11-22 create model v0.1
    [Каркас.stl, Корзина.stl, Рычаг.stl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]
2024-11-23 made new card
    [Требушет.stl]
2024-11-23 made new cart
    [readme.stl]
2024-11-24 trebuchet 3d model v0.9.1
    [Болт_М6_40_7798-70.stl, Винт рычага.stl, Гайка_М6_5915-70.stl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]
2024-12-03 add docs for kinematics
2024-12-03 fixed? weight mass counter
    [Болт_М6_40_7798-70.stl, Винт рычага.stl, Гайка_М6_5915-70.stl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]
2024-12-07 deleted trash
    [model.stl]
2024-12-07 add final version blueprint, mass center
    [Болт_М6_40_7798-70.stl, Гайка_М6_5915-70.stl, Каркас.stl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]
2024-12-07 пояснительная записка
2024-12-08 Пояснительная на отправку
2024-12-09 центр масс
2024-12-09 Пересчёт центра тяжести
